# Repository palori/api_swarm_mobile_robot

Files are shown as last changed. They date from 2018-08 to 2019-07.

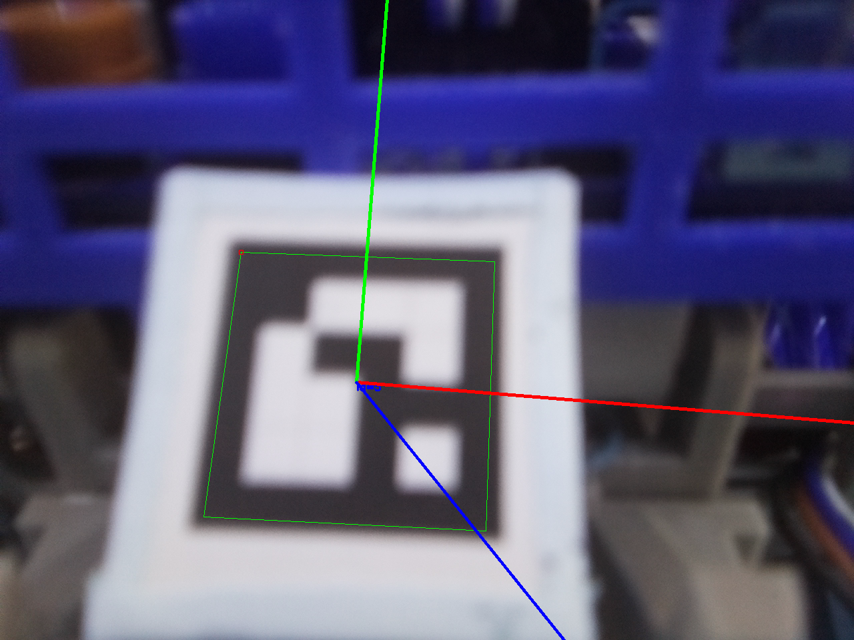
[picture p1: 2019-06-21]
API_rpi/image_proc/tests/aruco_test/pics/aruco_detected_12.png

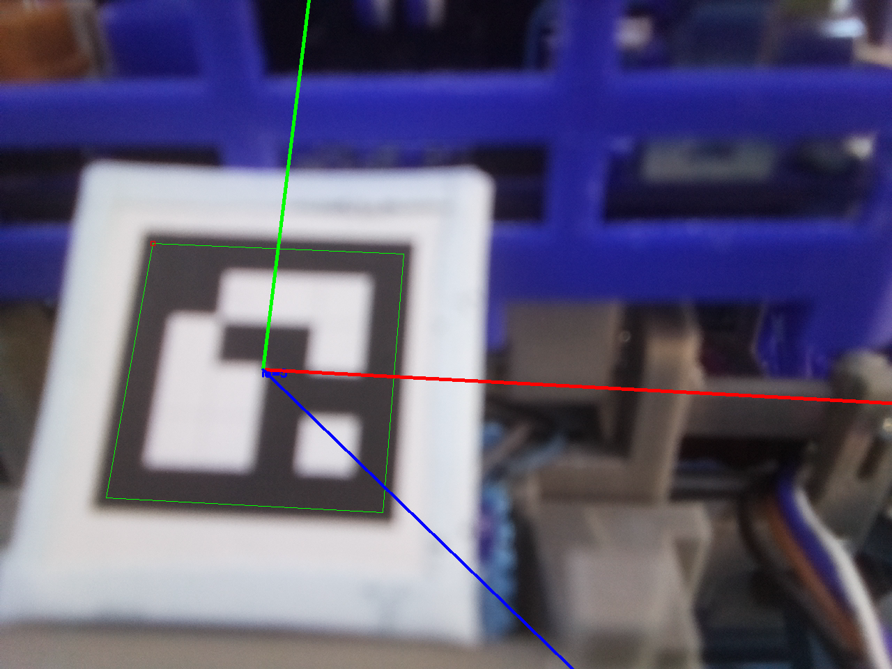
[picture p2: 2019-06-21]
API_rpi/image_proc/tests/aruco_test/pics/aruco_detected_11.png

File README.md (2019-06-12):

# api_swarm_mobile_robot
MSc Thesis: Multiple-mobile robot system.<br>
Institution: DenmarK Technical University (DTU)<br>
<br>
Authors:<br>
- Pau López Ribas<br>
- Imma Martínez Sellarès<br>
- Andrija Drk<br>
<br>
The project consists of designing. building and programming a multiple mobile robot system. It is developed to be 3 robots but it can easily be scaled up to more units.<br>
<br>
The project consists about:<br>
- `drawings` the design of the structure of the robots and the analysis of the forces<br>
- `hardware` physical components that form each robot<br>
- `software` the logic of the robots<br>
<br>

## Drawings
(still to write about)<br>
<br>

## Hardware
The hardware ... (still to work on it)<br>
2 boards<br>
Low level board: interaction with sensors (2 IR, 1 IMU, 2 encoders...)
                 and actuators (2 motors, 2 servos...)<br>
<br>

## Software
The software is divided in 2 groups (one for each board):<br>
- low-level<br>
- high-level<br>
<br>

## Matlab
...<br>
<br>

## Documents
...<br>
<br>

## Setup
Refer to the `readme.md` of the `setup` folder.<br>
<br>

## Executables
Refer to the `readme.md` of each executables folder.<br>
<br>

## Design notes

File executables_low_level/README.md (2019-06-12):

# Executables low-level board
...<br>
<br>
main_low_level.ino<br>
test folders arduino (now called `test_teensy_robot`)

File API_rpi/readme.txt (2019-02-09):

"pins.h" has nothing yet. Will contain the pins used in the Raspberry Pi.

"/demos_n_tests" contain examples you can run to test the libraries.

"/trash" contain old codes that are not used any more but than we would like to keep for some time.

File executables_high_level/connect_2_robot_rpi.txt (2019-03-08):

########################
# Connect to robot rpi #
########################

######################################################
## Useful links

- RSE WIKI, DTU Elektro Automation and Control department
  http://rsewiki.elektro.dtu.dk/index.php/Vision_based_Line_Follower

- Change Linux hostname
  https://www.howtogeek.com/167195/how-to-change-your-raspberry-pi-or-other-linux-devices-hostname/

- Mounting and unmounting using sshfs
  Mounnting is explained in a simplier way in some of the links from 'rse.wiki'
  https://help.ubuntu.com/community/SSHFS

######################################################
## Conect from a local network (hotspot...)

1. Turn on hotspot (now only in Pau's phone)

2. Connect the PC to that network

3. Check that at least 2 devices are connected (1 PC and at least 1 robot)
   - can check using ping:
     ping 192.168.43.N
                     138
                     38
                     174
                     ...

4. SSH the robot
   ssh -X user@192.168.43.N
   where user is the username of the robot (pi, local...)
   Introduce the password when asked for (egg, grenen, raspberry...)

5. Navigate to the folder where you have the script, compile it and run it
   cd ~/api_swarm_mobile_robot/API_rpi/image_proc/tests/detect_line		(might be another one)
   ls
   cmake .
   make
   ls 					(looking for the executable file to run, usually the green one)
   ./executable_file	(run the executable)

######################################################
## Conect from a local network (hotspot...)

1. Turn on hotspot (now only in Pau's phone)

2. Connect the PC to that network

3. Check that at least 2 devices are connected (1 PC and at least 1 robot)
   - can check using ping:
     ping 192.168.43.N
                     138
                     38
                     174
                     ...
          hostname.local
          cucumber.local		# cucumber would be the 'hostname' in this case
          ...

4. SSH the robot
   ssh -X user@192.168.43.N
   ssh -X user@hostname.local        # '.local' has nothing to do with the possible 'username'
   where 'user' is the username of the robot (pi, local...)
   Introduce the password when asked for (egg, grenen, raspberry...)

5. Navigate to the folder where you have the script, compile it and run it
   cd ~/api_swarm_mobile_robot/API_rpi/image_proc/tests/detect_line		(might be another one)
   ls
   cmake .
   make
   ls 					(looking for the executable file to run, usually the green one)
   ./executable_file	(run the executable)

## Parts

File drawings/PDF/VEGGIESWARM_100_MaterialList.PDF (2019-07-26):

34 | Screw M3x24 | DIN 7985 | | 4
33 | Screw M3x10 | DIN 7985 | | 4
32 | Screw M3x6 | DIN 7981 | | 34
31 | Screw M2,5x8 | DIN 7981 | | 2
30 | Screw M2,5x6 | DIN 7981 | | 16
29 | VEGGIESWARM_C113 | Rubber wheel D35 | Pololu | 5
28 | VEGGIESWARM_C112 | Axis D2 x 30 | Steel | 5
27 | VEGGIESWARM_C111 | Wheel adapter | Aluminium | 2
26 | VEGGIESWARM_C110 | Rubber wheel D90 | Pololu | 6
25 | VEGGIESWARM_C109 | Motor driver | Dual MC33926 | 1
24 | VEGGIESWARM_C108 | Plain bearing | JFM0608-04 | 2
23 | VEGGIESWARM_C107 | Battery | Lithium ion battery of 1100mAh and 12V | 1
22 | VEGGIESWARM_C106 | Motor 9.7:1 Metal Gearmotor 25Dx48L mm LP 6V with 48 CPR Encoder | Pololu | 2
21 | VEGGIESWARM_C105 | Camera Module | Raspberry Pi | 1
20 | VEGGIESWARM_C104 | IMU | MPU -6050 | 1
19 | VEGGIESWARM_C103 | Infrared sensor | Sharp 2Y0A 21F | 2
18 | VEGGIESWARM_C102 | High level board | Raspberry Pi 3 | 1
17 | VEGGIESWARM_C101 | RT Board | DTU | 1
16 | VEGGIESWARM_143_sym | Coupling 3 sym | PLA | 1
15 | VEGGIESWARM_143 | Coupling 3 | PLA | 1
14 | VEGGIESWARM_142 | Coupling 2 | PLA | 1
13 | VEGGIESWARM_141 | Coupling 1 | PLA | 1
12 | VEGGIESWARM_132_sym | Extension_sym | PLA | 1
11 | VEGGIESWARM_132 | Extension | PLA | 1
10 | VEGGIESWARM_131_sym | Extra wheels frame sym | PLA | 1
9 | VEGGIESWARM_131 | Extra wheels frame | PLA | 1
8 | VEGGIESWARM_123 | Back wheel frame | PLA | 1
7 | VEGGIESWARM_122 | Back wheel Support 2 | PLA | 1
6 | VEGGIESWARM_121 | Back wheel Support 1 | PLA | 1
5 | VEGGIESWARM_105 | Support motor driver | PLA | 1
4 | VEGGIESWARM_104 | Shell | PLA | 1
3 | VEGGIESWARM_103 | Camera support | PLA | 1
2 | VEGGIESWARM_102 | Lower frame | PLA | 1
1 | VEGGIESWARM_101 | Upper frame | PLA | 1
ITEM NO. | PART NUMBER | DESCRIPTION | MATERIAL | QTY.
Name Date Designed by IMMA 25/07/2019 Drawn by Checked by | Technical University of Denmark
Part Name Assembly Name | Project Name Design and build of a robot for the DTU RoboCup Doc Nr / Filename Scale Size A4 VEGGIESWARM_100_MaterialList

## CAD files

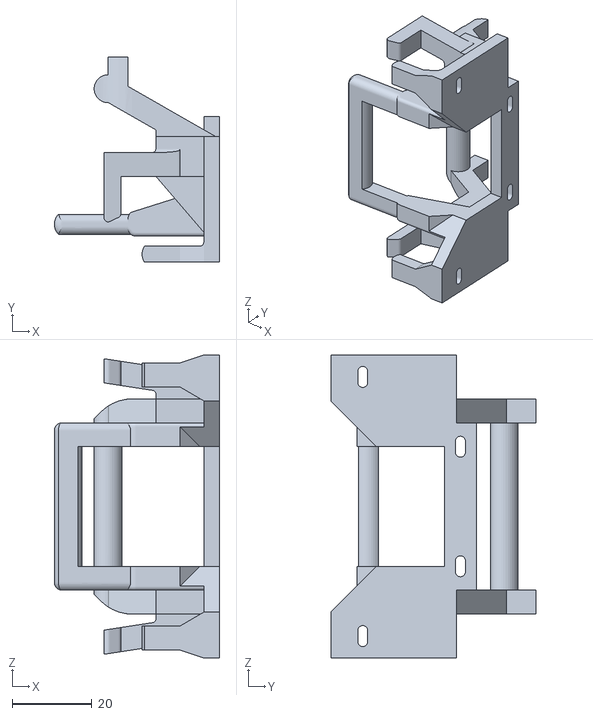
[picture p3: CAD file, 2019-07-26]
drawings/STL_Files/VEGGIESWARM_141_v4.STL
41.5 x 51.5 x 76.0

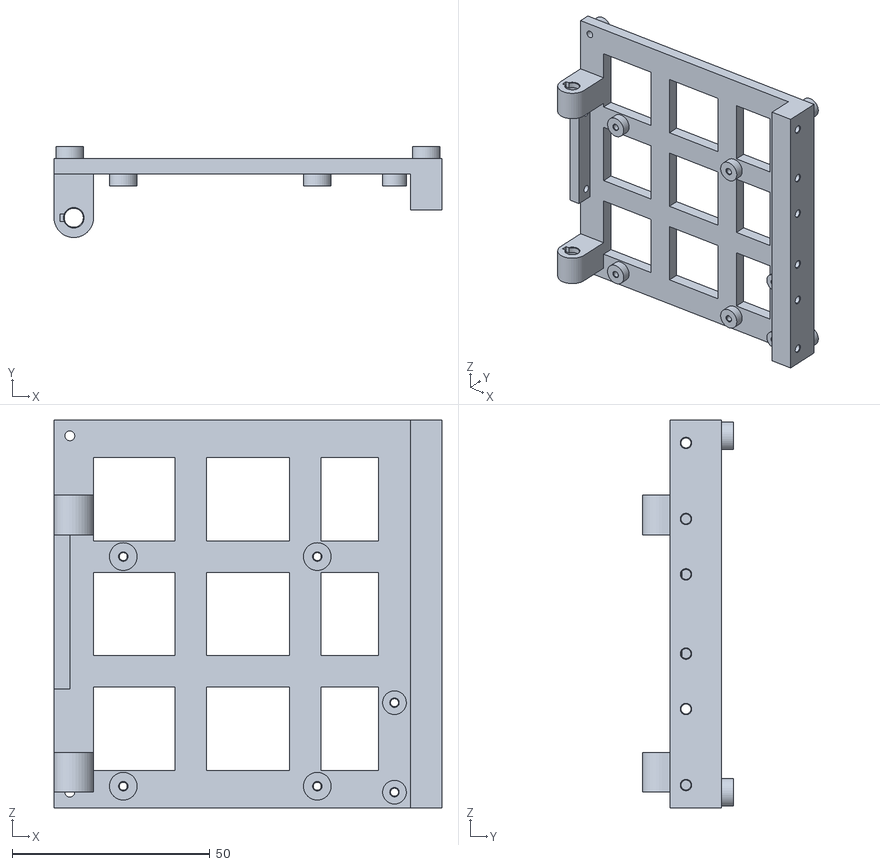
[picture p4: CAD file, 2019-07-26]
drawings/STL_Files/VEGGIESWARM_101.STL
98.0 x 23.0 x 98.0

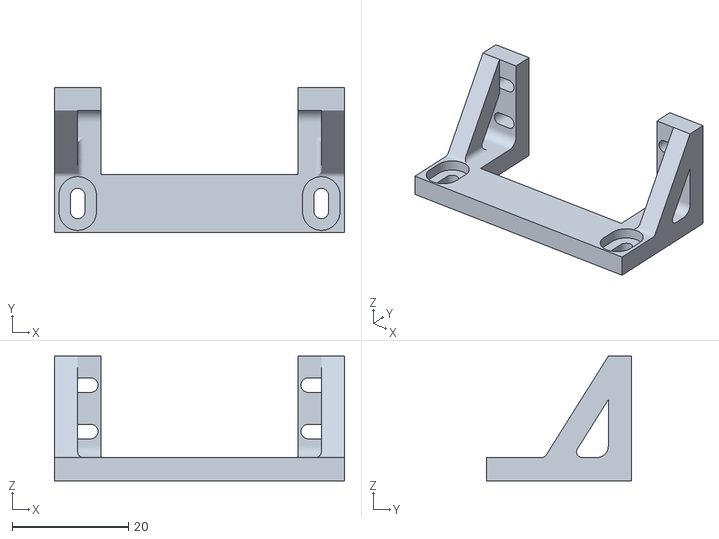
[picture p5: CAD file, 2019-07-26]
drawings/STL_Files/VEGGIESWARM_202.STL
50.0 x 25.0 x 21.5

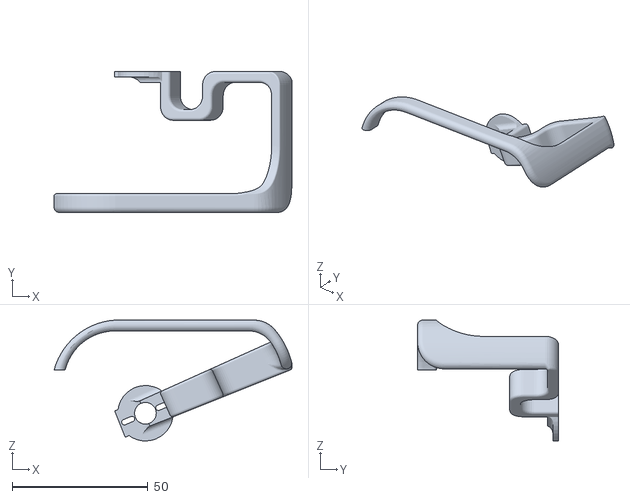
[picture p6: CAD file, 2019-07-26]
drawings/STL_Files/VEGGIESWARM_201.STL
87.7 x 52.0 x 44.5

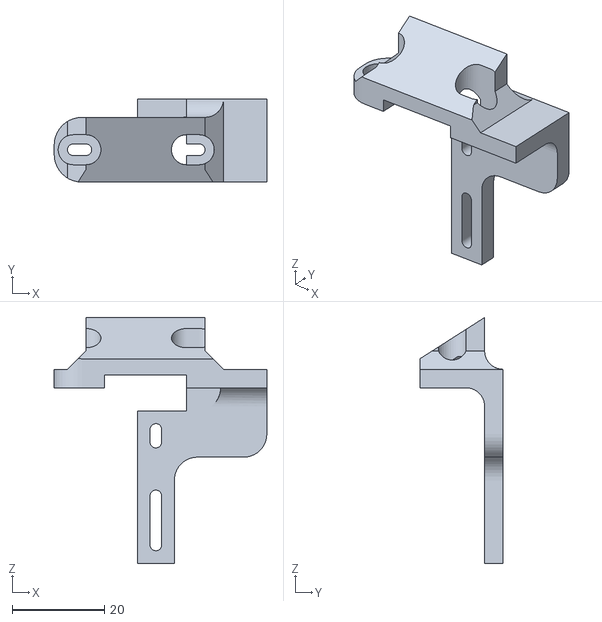
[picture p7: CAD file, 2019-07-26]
drawings/STL_Files/VEGGIESWARM_132_v1.STL
46.0 x 18.0 x 53.2

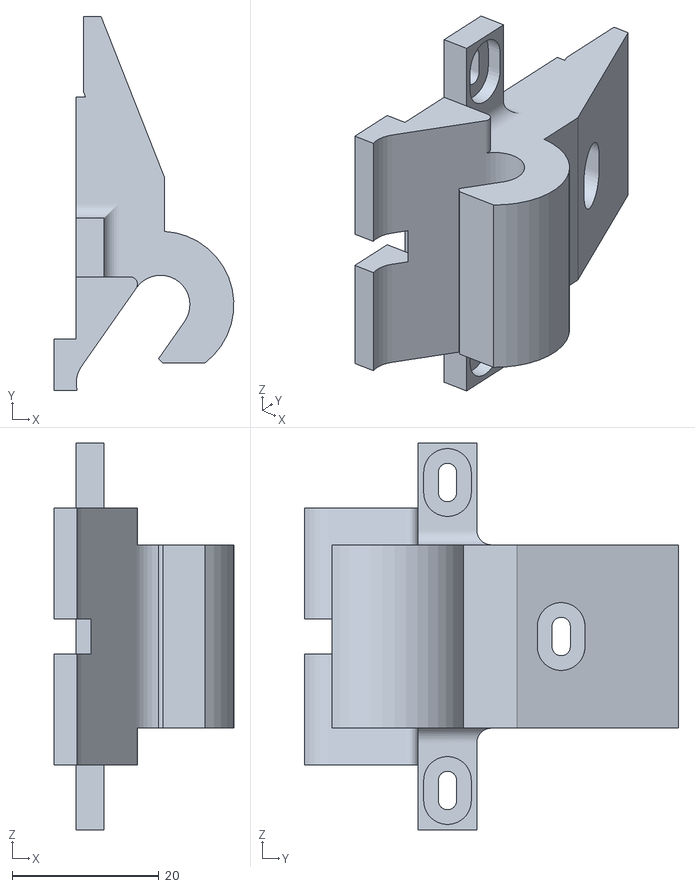
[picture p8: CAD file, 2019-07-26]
drawings/STL_Files/VEGGIESWARM_142_v4.STL
24.5 x 51.0 x 52.8

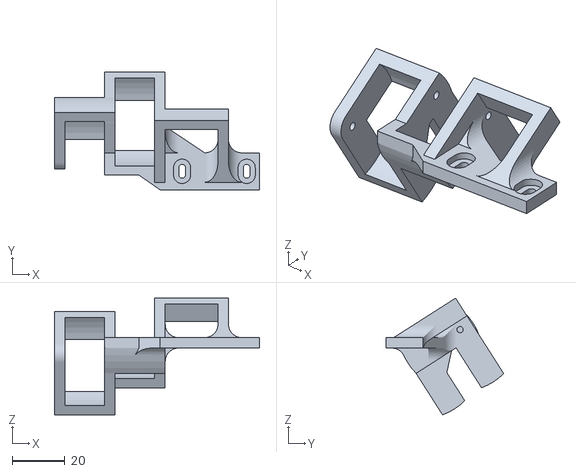
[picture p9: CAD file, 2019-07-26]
drawings/STL_Files/VEGGIESWARM_131_v3.STL
77.8 x 44.6 x 44.3

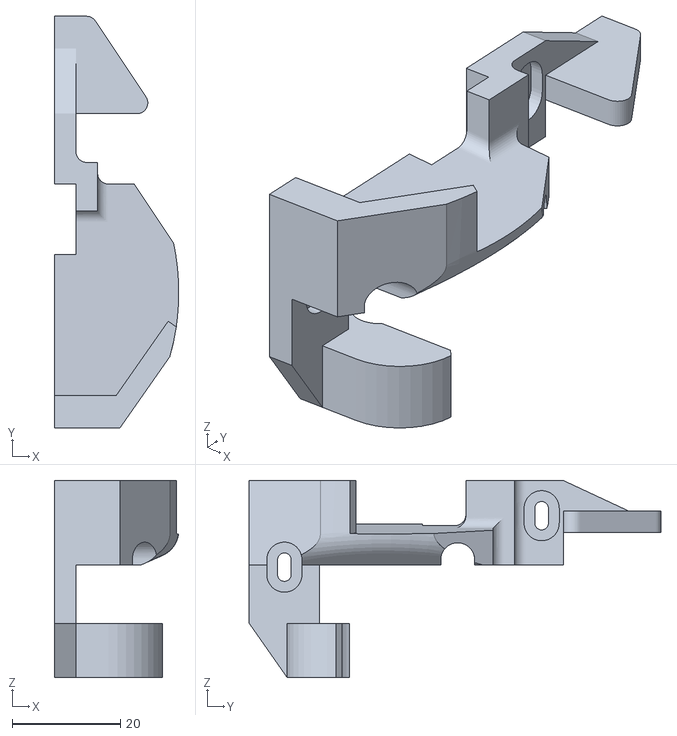
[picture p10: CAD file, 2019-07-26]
drawings/STL_Files/VEGGIESWARM_143_v4.STL
23.0 x 76.0 x 36.4

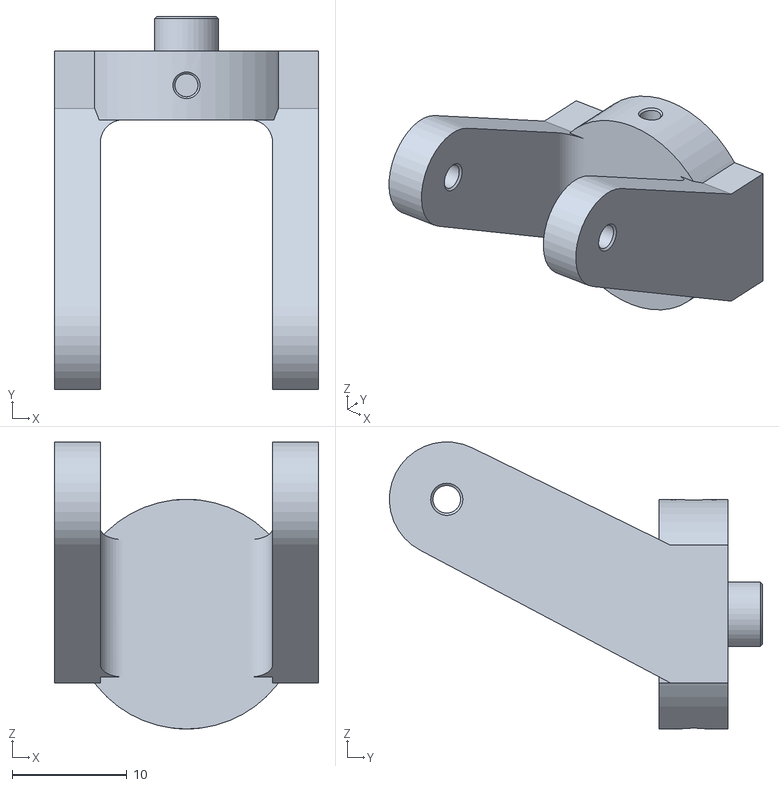
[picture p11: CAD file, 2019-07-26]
drawings/STL_Files/VEGGIESWARM_123_v3.STL
23.0 x 32.5 x 25.0

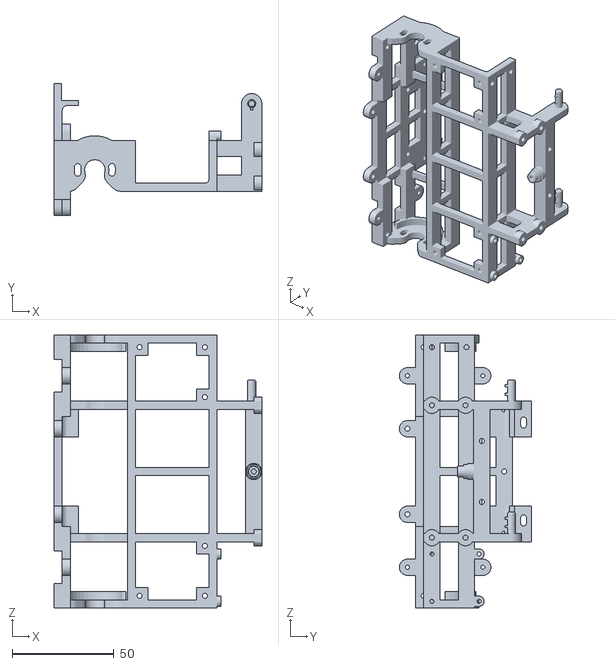
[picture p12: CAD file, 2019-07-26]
drawings/STL_Files/VEGGIESWARM_102_v3.STL
102.0 x 65.0 x 134.0

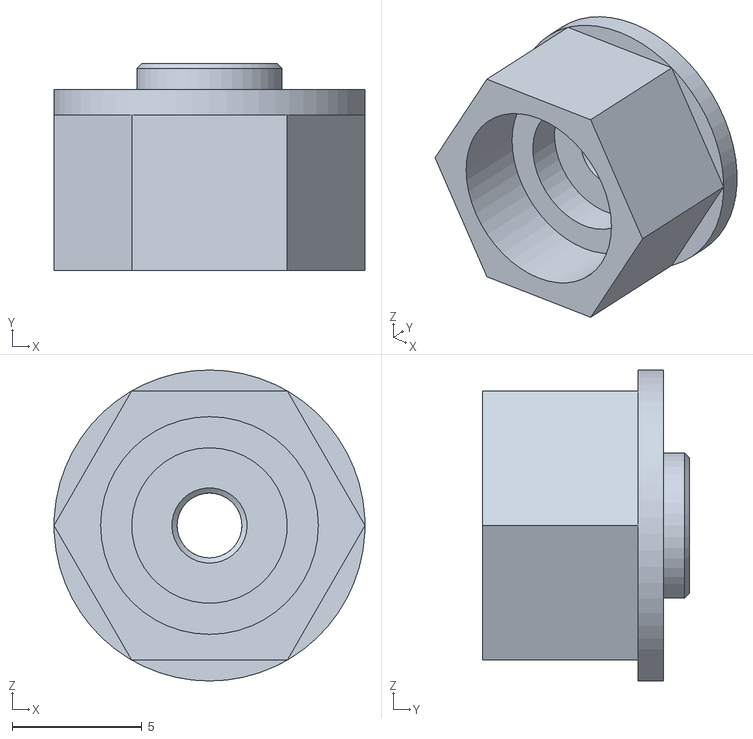
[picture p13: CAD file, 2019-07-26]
drawings/STL_Files/VEGGIESWARM_121_v3.STL
12.0 x 8.00 x 12.0

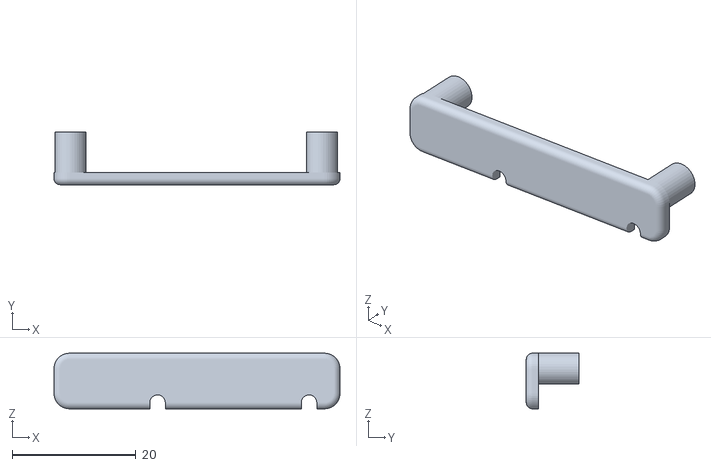
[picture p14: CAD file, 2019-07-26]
drawings/STL_Files/VEGGIESWARM_104.STL
46.2 x 8.50 x 9.00

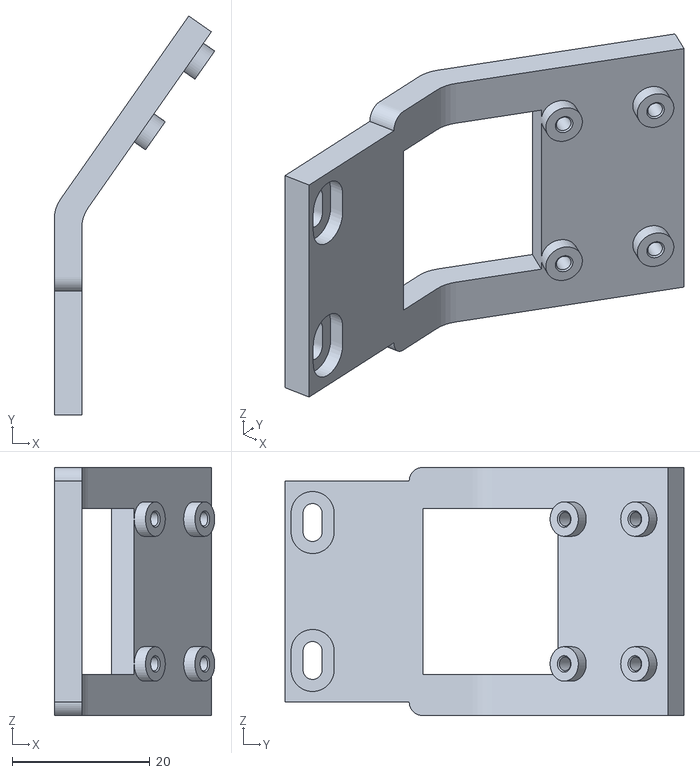
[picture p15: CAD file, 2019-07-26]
drawings/STL_Files/VEGGIESWARM_103_v1.STL
23.3 x 57.9 x 36.0

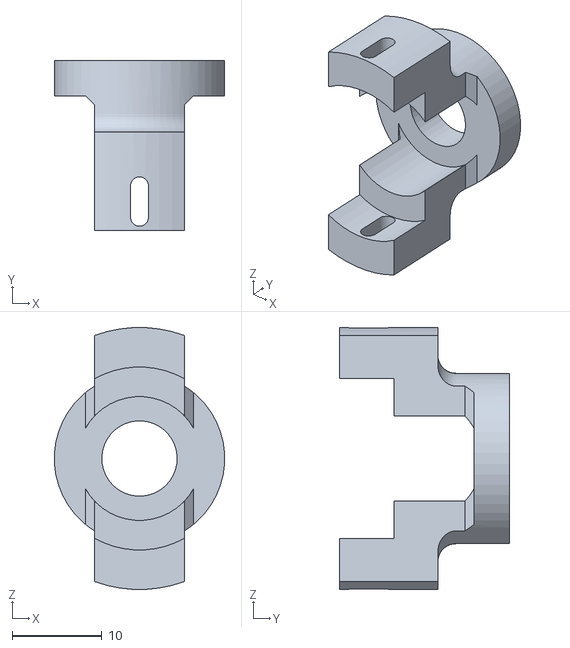
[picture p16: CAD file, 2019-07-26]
drawings/STL_Files/VEGGIESWARM_122_v4.STL
19.0 x 19.0 x 29.2

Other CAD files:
drawings/STL_Files/VEGGIESWARM_143_v4_sym.STL
drawings/STL_Files/VEGGIESWARM_131_v3_sym.STL

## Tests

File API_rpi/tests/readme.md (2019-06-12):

# Tests
The paths to the files in the `Makefile` / `CMakeLists.txt` for each test must be updated. It will not compile now :)<br>
<br>
Also bear in mind that some functions from the libraries might have been updated and might remain unchanged in the tests making them fail when attempting to compile.

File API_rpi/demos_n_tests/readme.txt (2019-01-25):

**************
* readme.txt *
**************

Run shell scripts to compile and run the tests from the terminal.
(Eg.: sh filename.sh)

To make it executable just type in the terminal:
chmod +x filename.sh

Then you will be able to run it also with this command:
./filename

It automatically deletes the executable files after showing the results in the terminal to keep the folder organized.
If the demo/test contains a while true, then the 'executable' is moved to the folder "/executables".

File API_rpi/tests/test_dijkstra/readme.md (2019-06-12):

# Test Dijkstra
Not working due to some changes in how to call the functions.<br>
Only need to be changed `main_dijkstra.cpp`.

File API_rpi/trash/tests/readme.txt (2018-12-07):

**************
* readme.txt *
**************

Run shell scripts to compile and run the tests from the terminal.
(Eg.: sh my_script.sh) 

It automatically deletes the executable files after showing the results in the terminal to keep the folder organized.

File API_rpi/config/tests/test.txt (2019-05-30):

name, task_type, num_robots
take_picture, 1, 1
up-stairs, 2, 3

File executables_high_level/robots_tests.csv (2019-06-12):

agent | id | hostname | ip | port_info | port_image | port_task
master | 0 | ginger | localhost | 7999 | 7998 | 7997
robot | 1 | ginger | localhost | 8000 | 7000 | 7010
robot | 2 | ginger | localhost | 8001 | 7001 | 7011
robot | 3 | ginger | localhost | 8002 | 7002 | 7012
# last row is never read

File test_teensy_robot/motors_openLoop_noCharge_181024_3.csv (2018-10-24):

Time | Vel1 | Vel2 | SP1 | SP2 | Out1 | Out2
18.82 | 0.00 | 0.00 | 0.10 | 0.10 | 0.40 | 0.40
19.83 | 0.00 | 0.00 | 0.10 | 0.10 | 0.40 | 0.40
19.84 | 0.00 | 0.00 | 0.10 | 0.10 | 0.40 | 0.40
19.85 | 0.00 | 0.06 | 0.10 | 0.10 | 0.40 | 0.40
19.86 | 0.00 | 0.00 | 0.10 | 0.10 | 0.40 | 0.40
19.87 | 0.00 | 0.00 | 0.10 | 0.10 | 0.40 | 0.40
19.89 | 0.00 | 0.00 | 0.10 | 0.10 | 0.40 | 0.40
19.90 | 0.00 | 0.00 | 0.10 | 0.10 | 0.40 | 0.40
19.91 | 0.00 | 0.00 | 0.10 | 0.10 | 0.40 | 0.40
19.92 | 0.00 | 0.00 | 0.10 | 0.10 | 0.40 | 0.40
19.93 | 0.00 | 0.00 | 0.10 | 0.10 | 0.40 | 0.40
19.94 | 0.00 | 0.00 | 0.10 | 0.10 | 0.40 | 0.40
19.95 | 0.00 | 0.00 | 0.10 | 0.10 | 0.40 | 0.40
19.96 | 0.00 | 0.00 | 0.10 | 0.10 | 0.40 | 0.40
19.97 | 0.00 | 0.00 | 0.10 | 0.10 | 0.40 | 0.40
19.98 | 0.00 | 0.00 | 0.10 | 0.10 | 0.40 | 0.40
19.99 | 0.00 | 0.00 | 0.10 | 0.10 | 0.40 | 0.40
20.00 | 0.00 | 0.00 | 0.10 | 0.10 | 0.40 | 0.40
20.01 | 0.00 | 0.00 | 0.10 | 0.10 | 0.40 | 0.40
20.02 | 0.00 | 0.00 | 0.10 | 0.10 | 0.40 | 0.40
20.03 | 0.00 | 0.00 | 0.10 | 0.10 | 0.40 | 0.40
20.04 | 0.00 | 0.00 | 0.10 | 0.10 | 0.40 | 0.40
20.05 | 0.00 | 0.00 | 0.10 | 0.10 | 0.40 | 0.40
20.06 | 0.00 | 0.00 | 0.10 | 0.10 | 0.40 | 0.40
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

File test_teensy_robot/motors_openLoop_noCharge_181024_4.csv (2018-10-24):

Time | Vel1 | Vel2 | SP1 | SP2 | Out1 | Out2
14.40 | 0.00 | 0.00 | 0.10 | 0.10 | 0.10 | 0.10
15.41 | 0.00 | 0.00 | 0.10 | 0.10 | 0.10 | 0.10
15.42 | 0.00 | 0.00 | 0.10 | 0.10 | 0.10 | 0.10
15.43 | 0.00 | 0.00 | 0.10 | 0.10 | 0.10 | 0.10
15.44 | 0.00 | 0.00 | 0.10 | 0.10 | 0.10 | 0.10
15.45 | 0.00 | 0.00 | 0.10 | 0.10 | 0.10 | 0.10
15.46 | 0.00 | 0.00 | 0.10 | 0.10 | 0.10 | 0.10
15.47 | 0.00 | 0.00 | 0.10 | 0.10 | 0.10 | 0.10
15.48 | 0.00 | 0.00 | 0.10 | 0.10 | 0.10 | 0.10
15.49 | 0.00 | 0.00 | 0.10 | 0.10 | 0.10 | 0.10
15.50 | 0.00 | 0.00 | 0.10 | 0.10 | 0.10 | 0.10
15.51 | 0.00 | 0.00 | 0.10 | 0.10 | 0.10 | 0.10
15.52 | 0.00 | 0.00 | 0.10 | 0.10 | 0.10 | 0.10
15.53 | 0.00 | 0.00 | 0.10 | 0.10 | 0.10 | 0.10
15.54 | 0.00 | 0.00 | 0.10 | 0.10 | 0.10 | 0.10
15.55 | 0.00 | 0.00 | 0.10 | 0.10 | 0.10 | 0.10
15.56 | 0.00 | 0.00 | 0.10 | 0.10 | 0.10 | 0.10
15.57 | 0.00 | 0.00 | 0.10 | 0.10 | 0.10 | 0.10
15.58 | 0.00 | 0.00 | 0.10 | 0.10 | 0.10 | 0.10
15.59 | 0.00 | 0.00 | 0.10 | 0.10 | 0.10 | 0.10
15.60 | 0.00 | 0.00 | 0.10 | 0.10 | 0.10 | 0.10
15.61 | 0.00 | 0.00 | 0.10 | 0.10 | 0.10 | 0.10
15.62 | 0.00 | 0.00 | 0.10 | 0.10 | 0.10 | 0.10
15.64 | 0.00 | 0.00 | 0.10 | 0.10 | 0.10 | 0.10
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

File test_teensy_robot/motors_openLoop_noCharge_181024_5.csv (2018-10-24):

Time | Vel1 | Vel2 | SP1 | SP2 | Out1 | Out2
7.36 | 0.00 | 0.00 | 0.10 | 0.10 | 0.40 | 0.40
8.37 | 0.00 | 0.00 | 0.10 | 0.10 | 0.40 | 0.40
8.38 | 0.00 | 0.06 | 0.10 | 0.10 | 0.40 | 0.40
8.39 | 0.00 | 0.11 | 0.10 | 0.10 | 0.40 | 0.40
8.40 | 0.00 | 0.00 | 0.10 | 0.10 | 0.40 | 0.40
8.41 | 0.00 | 0.12 | 0.10 | 0.10 | 0.40 | 0.40
8.42 | 0.00 | 0.11 | 0.10 | 0.10 | 0.40 | 0.40
8.43 | 0.00 | 0.12 | 0.10 | 0.10 | 0.40 | 0.40
8.44 | 0.00 | 0.18 | 0.10 | 0.10 | 0.40 | 0.40
8.45 | 0.00 | 0.11 | 0.10 | 0.10 | 0.40 | 0.40
8.46 | 0.00 | 0.12 | 0.10 | 0.10 | 0.40 | 0.40
8.47 | 0.00 | 0.18 | 0.10 | 0.10 | 0.40 | 0.40
8.48 | 0.00 | 0.11 | 0.10 | 0.10 | 0.40 | 0.40
8.49 | 0.00 | 0.18 | 0.10 | 0.10 | 0.40 | 0.40
8.50 | 0.00 | 0.12 | 0.10 | 0.10 | 0.40 | 0.40
8.51 | 0.00 | 0.17 | 0.10 | 0.10 | 0.40 | 0.40
8.52 | 0.00 | 0.12 | 0.10 | 0.10 | 0.40 | 0.40
8.53 | 0.00 | 0.17 | 0.10 | 0.10 | 0.40 | 0.40
8.54 | 0.00 | 0.18 | 0.10 | 0.10 | 0.40 | 0.40
8.55 | 0.00 | 0.12 | 0.10 | 0.10 | 0.40 | 0.40
8.56 | 0.00 | 0.17 | 0.10 | 0.10 | 0.40 | 0.40
8.57 | 0.00 | 0.18 | 0.10 | 0.10 | 0.40 | 0.40
8.58 | 0.00 | 0.12 | 0.10 | 0.10 | 0.40 | 0.40
8.59 | 0.00 | 0.17 | 0.10 | 0.10 | 0.40 | 0.40
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

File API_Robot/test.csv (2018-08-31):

A | 1
b | 2
d | 40

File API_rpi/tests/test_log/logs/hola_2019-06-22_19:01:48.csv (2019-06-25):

1561222908181 | Bon dia!
1561222908181 | Bona nit :)

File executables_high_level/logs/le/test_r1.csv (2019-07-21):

timestamp | robot_id | robot_a_id | robot_b_id | robot_a_alive | robot_b_alive | leader | trigger | i_detected | is_election | robots_ids | proposed_leader
1561248971172 | 1 | 2 | 3 | 0 | 0 | 0 | 1 | 0 | 0
1561248971423 | 1 | 2 | 3 | 0 | 0 | 1 | 0 | 0 | 0
1561248971673 | 1 | 2 | 3 | 0 | 0 | 1 | 0 | 0 | 0
1561248971923 | 1 | 2 | 3 | 0 | 0 | 1 | 0 | 0 | 0
1561248972173 | 1 | 2 | 3 | 1 | 1 | 1 | 1 | 0 | 0 | 3 | 1
1561248972424 | 1 | 2 | 3 | 1 | 1 | 1 | 1 | 0 | 0 | 3;1;2 | 1
1561248972674 | 1 | 2 | 3 | 1 | 1 | 1 | 1 | 0 | 0 | 3;1;2 | 1
1561248972924 | 1 | 2 | 3 | 1 | 1 | 1 | 1 | 0 | 0 | 3;1;2 | 1
1561248973174 | 1 | 2 | 3 | 1 | 1 | 1 | 1 | 0 | 0 | 3;1;2 | 1
1561248973425 | 1 | 2 | 3 | 1 | 1 | 1 | 1 | 0 | 0 | 3;1;2 | 1
1561248973675 | 1 | 2 | 3 | 1 | 1 | 1 | 1 | 0 | 0 | 3;1;2 | 1
1561248973925 | 1 | 2 | 3 | 1 | 1 | 1 | 1 | 0 | 0 | 3;1;2 | 1
1561248974175 | 1 | 2 | 3 | 1 | 1 | 1 | 1 | 0 | 0 | 3;1;2 | 1
1561248974425 | 1 | 2 | 3 | 1 | 1 | 1 | 0 | 0 | 0
1561248974676 | 1 | 2 | 3 | 1 | 1 | 1 | 0 | 0 | 0
1561248974926 | 1 | 2 | 3 | 1 | 1 | 1 | 0 | 0 | 0
1561248975176 | 1 | 2 | 3 | 1 | 1 | 1 | 0 | 0 | 0
1561248975426 | 1 | 2 | 3 | 1 | 1 | 1 | 0 | 0 | 0
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

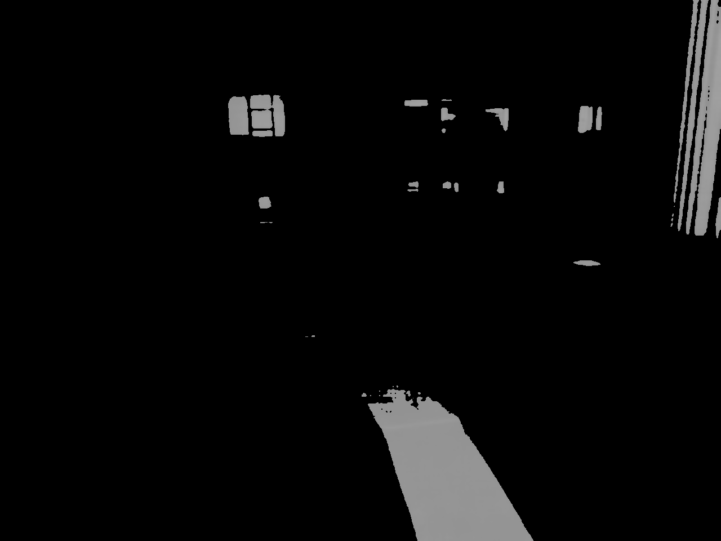
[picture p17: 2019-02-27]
API_rpi/image_proc/tests/images/img_bin_ycbcr2.png

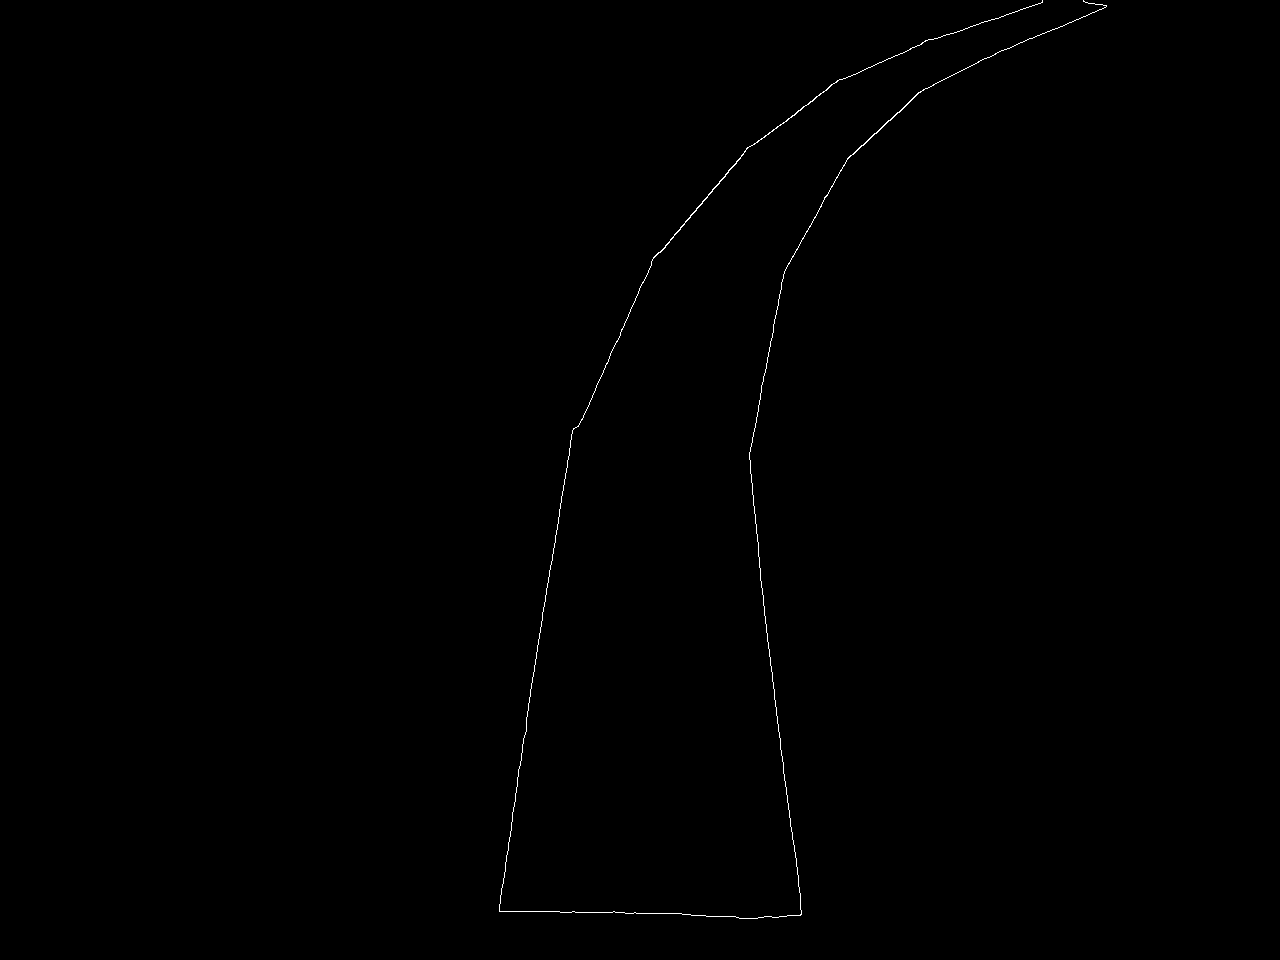
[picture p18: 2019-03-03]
API_rpi/image_proc/tests/images/img_edge.png

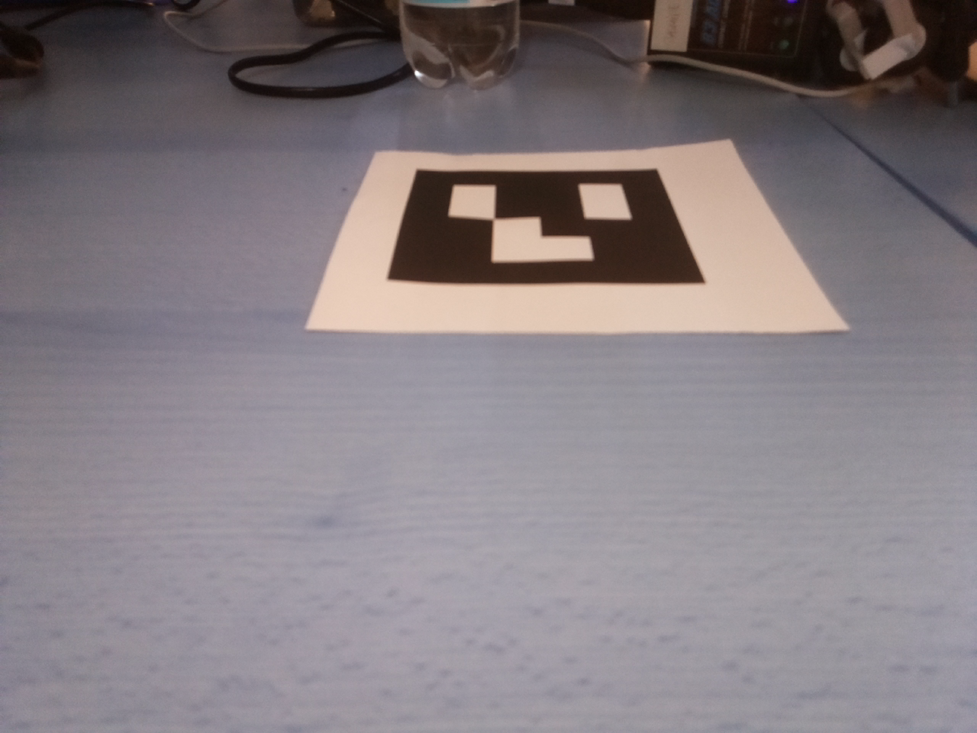
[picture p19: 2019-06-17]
API_rpi/image_proc/tests/aruco_test/pics/aruco_0.png

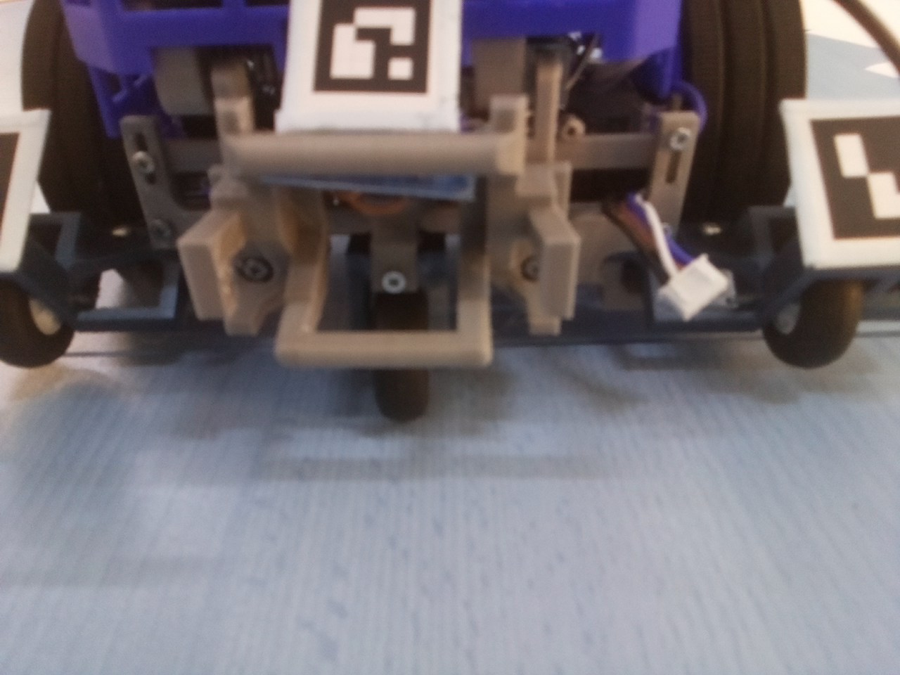
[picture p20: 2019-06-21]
API_rpi/image_proc/tests/aruco_test/pics/aruco_detected_5.png

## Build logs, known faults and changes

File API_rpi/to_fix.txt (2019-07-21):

To fix
------
sensors.x (item -> items)
attr & methods -> public and private

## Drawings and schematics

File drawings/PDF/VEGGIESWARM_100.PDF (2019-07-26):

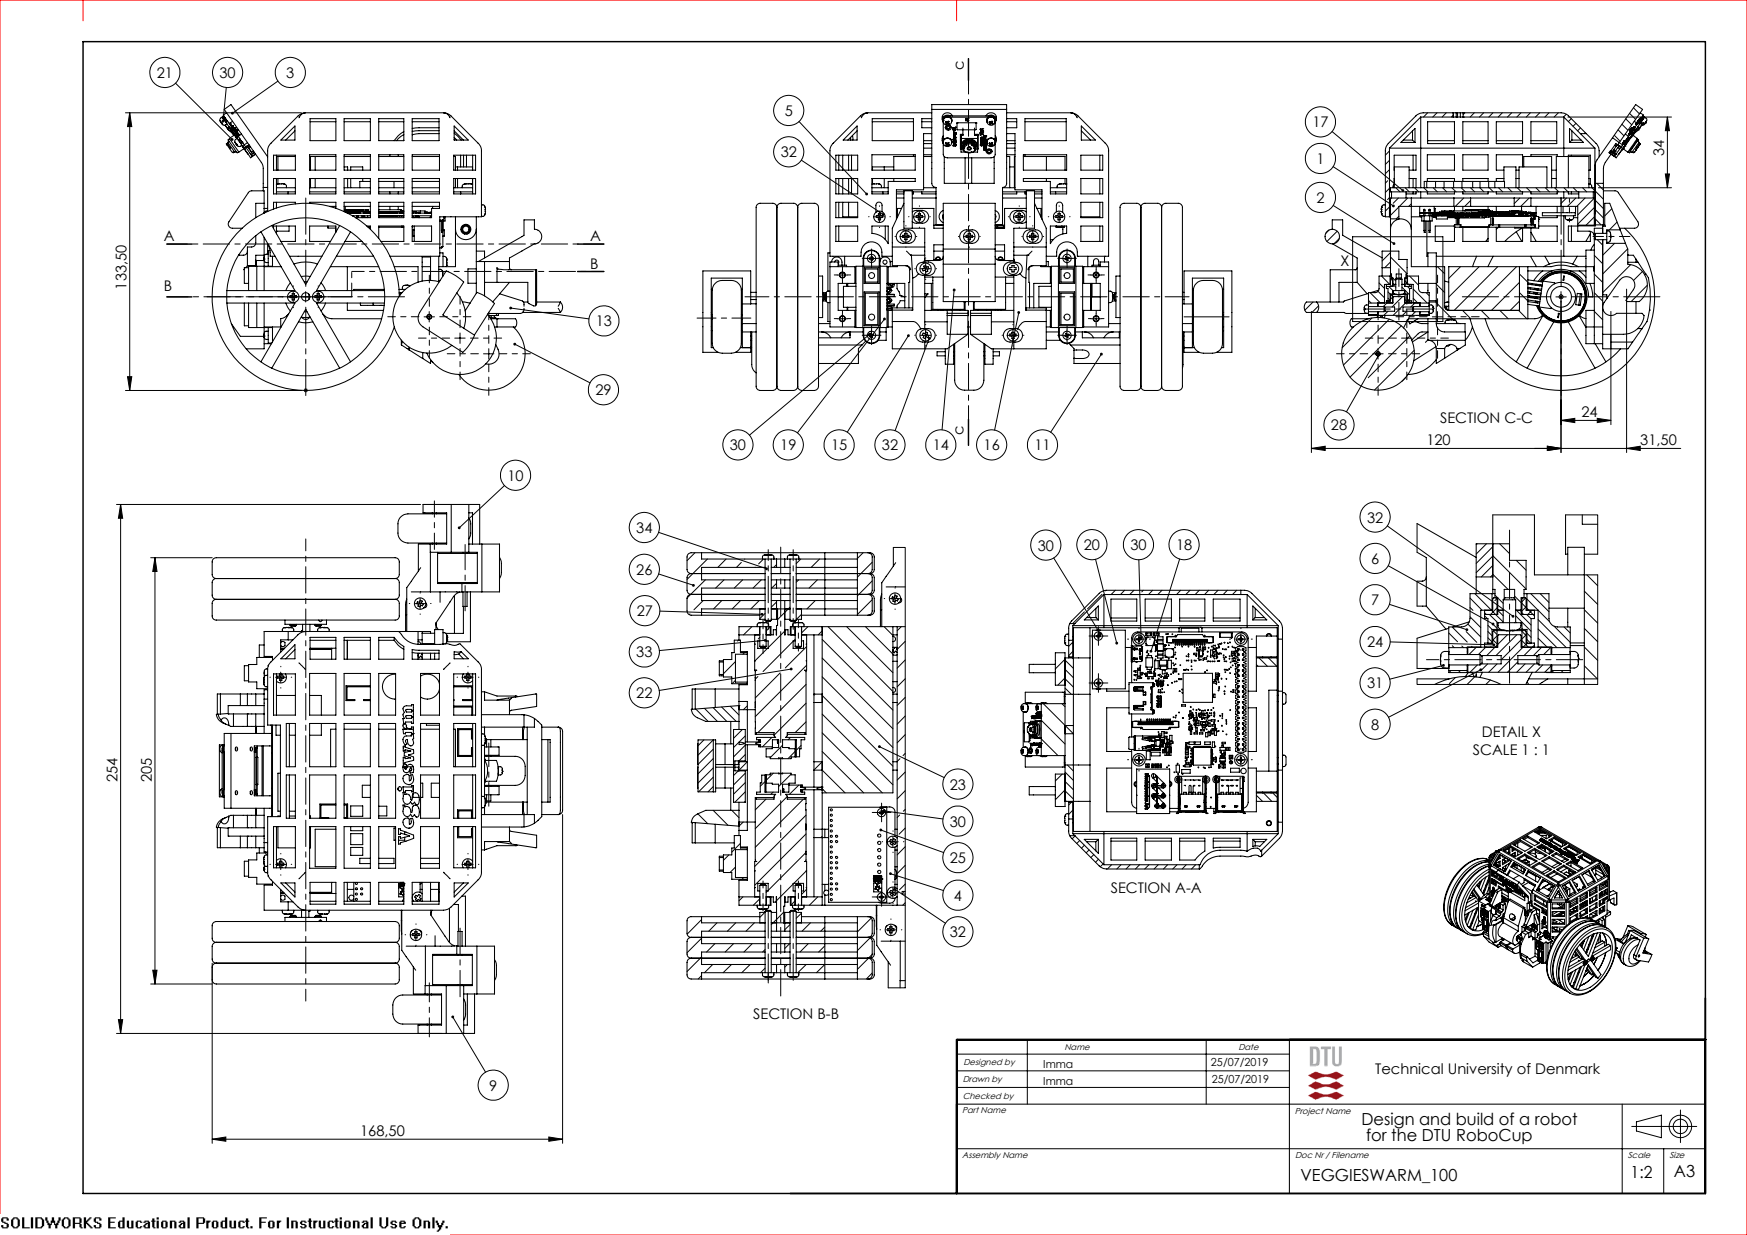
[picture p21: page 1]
SECTION A-A; SECTION C-C; SECTION B-B; DETAIL X SCALE 1 : 1; Assembly Name; Part Name; Checked by; Drawn by; Designed by; Technical University of Denmark Imma

Project Name
Design and build of a robot
for the DTU RoboCup
VEGGIESWARM_100

Doc Nr / Filename

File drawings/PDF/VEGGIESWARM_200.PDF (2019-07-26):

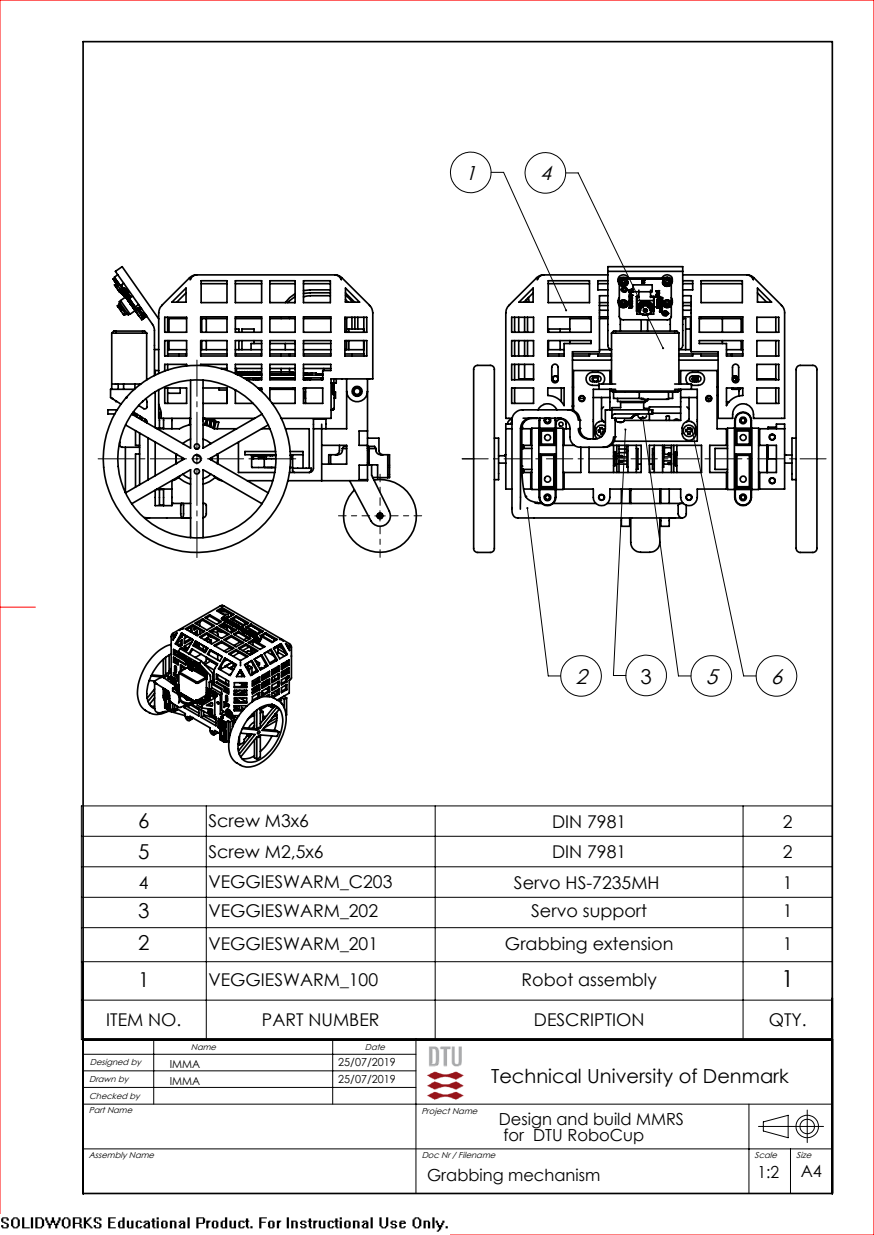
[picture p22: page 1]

6 | Screw M3x6 | DIN 7981 | 2
5 | Screw M2,5x6 | DIN 7981 | 2
4 | VEGGIESWARM_C203 | Servo HS-7235MH | 1
3 | VEGGIESWARM_202 | Servo support | 1
2 | VEGGIESWARM_201 | Grabbing extension | 1
1 | VEGGIESWARM_100 | Robot assembly | 1
ITEM NO. | PART NUMBER | DESCRIPTION | QTY.

Name Date Designed by IMMA 25/07/2019 IMMA 25/07/2019 Drawn by Checked by | Technical University of Denmark

Part Name Assembly Name | Project Name Design and build MMRS for DTU RoboCup Doc Nr / Filename Scale Size A4 Grabbing mechanism 1:2

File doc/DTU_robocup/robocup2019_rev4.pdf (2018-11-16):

2 | 1 | | 3 13 | 7

### start

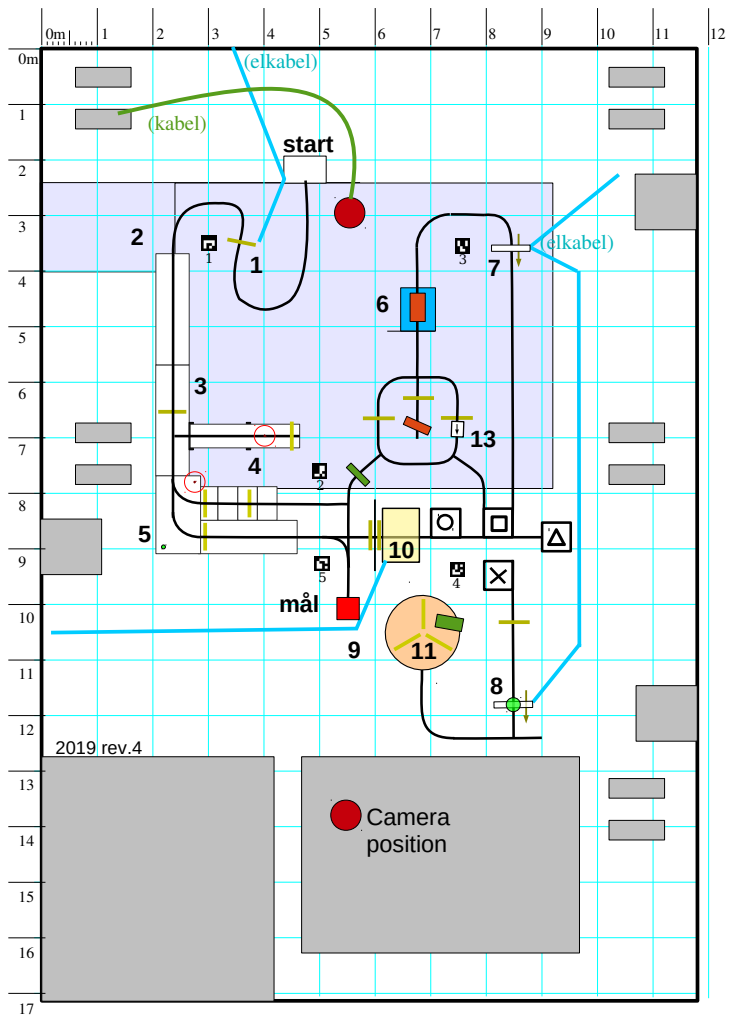
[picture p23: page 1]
2019 rev.4; mål; (elkabel); (kabel)

Camera position

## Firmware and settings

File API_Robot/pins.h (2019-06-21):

#ifndef PINS_H
#define PINS_H


#define USING_ARDUINO // flag to see if need to include Arduino library or not
// Simplier version than the original from JCA.
// Teensy 3.5
//////////////////////////////////////////////////////////////////////////////////

// Pin Definitions for Regbot v4.1 2018

//Motor names

#define LEFT_MOTOR 1
#define RIGHT_MOTOR 2

// Main pins
#define PIN_LED_STATUS          11
#define PIN_LED_DEBUG           13
#define PIN_START_BUTTON        26
#define PIN_LINE_LED_HIGH       12
#define PIN_LINE_LED_LOW        25
#define PIN_DISABLE2            7//27
#define PIN_POWER_IR            24
#define PIN_POWER_ROBOT         28

// ADC pins
#define ADC_NUM_NO_LS           5
#define ADC_NUM_ALL             (ADC_NUM_NO_LS + 8)
//
#define PIN_IR_RAW_1            A1
#define PIN_IR_RAW_2            A0
#define PIN_BATTERY_VOLTAGE     A14
#define PIN_LEFT_MOTOR_CURRENT  31//A2
#define PIN_RIGHT_MOTOR_CURRENT 32//A3
//
#define PIN_LINE_SENSOR_0       A12
#define PIN_LINE_SENSOR_1       A13
#define PIN_LINE_SENSOR_2       A15
#define PIN_LINE_SENSOR_3       A16
#define PIN_LINE_SENSOR_4       A17
#define PIN_LINE_SENSOR_5       A18
#define PIN_LINE_SENSOR_6       A19
#define PIN_LINE_SENSOR_7       A20

// Motor Controller pins
#define PIN_LEFT_DIR            37//6
#define PIN_LEFT_PWM            35//3
#define PIN_RIGHT_PWM           36//4
#define PIN_RIGHT_DIR           38//2

#define PIN_LEFT_ENCODER_A      23
#define PIN_LEFT_ENCODER_B      22
#define PIN_RIGHT_ENCODER_A     20
#define PIN_RIGHT_ENCODER_B     21
#define M1DIR           PIN_LEFT_DIR // M1IN2 - Teensy Digital (direction)
#define M1PWM           PIN_LEFT_PWM // M1IN1 - Teensy Digital (PWM)
#define M2DIR3          PIN_RIGHT_DIR // M2IN2 - Teensy Digital (direction) hardware 3 only
#define M2PWM3          PIN_RIGHT_PWM // M2IN1 - Teensy Digital (PWM) hardware 3
#define M12DIS          PIN_DISABLE2 // M1+M2 D2  enable both motors - hardware 3 only
#define M1ENC_A         PIN_LEFT_ENCODER_A // Encoder A - Teensy Digital
#define M1ENC_B         PIN_LEFT_ENCODER_B // Encoder B - Teensy Digital
#define M2ENC_A         PIN_RIGHT_ENCODER_A // Encoder A - Teensy Digital
#define M2ENC_B         PIN_RIGHT_ENCODER_B // Encoder B - Teensy Digital
// Legacy pins (only used < 3)
#define M1DIS1          4 // M1D2  - Teensy Digital 4 (disable (hiz))) - hardware < 3
#define M2DIS1          10 // M2D2  - Teensy Digital 10 (disable (hi-z)) - hardware < 3
#define M2PWM1          9 // M2IN1 - Teensy Digital 9 (PWM) hardware < 3
#define SLEW            7 // SLEW  - Teensy Digital 7  -  hardware 1 og 2 only, hardware 3 fixed high
#define M2DIR1          8 // M2IN2 - Teensy Digital 8 (direction) hardware < 3 only

// Servo pins
#define PIN_SERVO1      5 // Teensy pin for servo 1
#define PIN_SERVO2      9 // Teensy pin for servo 2
#define PIN_SERVO3      10 // Teensy pin for servo 3
#define PIN_SERVO4      29 // Teensy pin for servo 4
#define PIN_SERVO5      30 // Teensy pin for servo 5 (Shared with Buzzer!)
#define SERVO_PIN_0     PIN_SERVO4 // Deprecated!
#define SERVO_PIN_1     PIN_SERVO5 // Deprecated!
#define PIN_BUZZER		30 // Shared with SERVO5!

#endif

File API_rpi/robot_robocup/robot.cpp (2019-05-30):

#include "robot.h"

Robot::Robot(){
	//params.hostname.set("localhost");

	this->hostname_master.set("localhost");

	Robot_params rp("test",1,2,3,4,5,10);
	this->params = rp;

	/*Publisher pub(this->params.port_image.get());
	pub.disconnect();
	pub_image_task = pub;
	pub_image_task.setup();

	Publisher pub1(this->params.port_info.get());
	pub1.disconnect();
	pub_robot_info = pub1;
	pub_robot_info.setup();*/

	//pub_image_task(this->params.port_image.get());
	//pub_robot_info(this->params.port_info.get());

	pub_image_task.set_port(this->params.port_image.get());
	pub_image_task.setup();

	pub_robot_info.set_port(this->params.port_image.get());
	pub_robot_info.setup();

	run_mission.set(false);
}

Robot::~Robot(){}


/*/ probably never used...
Robot::Robot(string hostname){ // params from other 2 robots (port and hostname)
	//Subscriber subs_robot_a();
	//Subscriber subs_robot_b();
	Robot_params rp(hostname,5000,20);
	this->params = rp;
	//this->params(hostname,1,2,3,4,5,10);
	//params.hostname.set(hostname);
	//cout << "hostname: " << this->params.hostname.get_last_item() << endl;

}*/

// always use this one
Robot::Robot(string hostname_master, string hostname, string hostname_a, string hostname_b, int max_len, int port_image, int port_task, int port_info, int port_info_robot_a, int port_info_robot_b){
	//cout << "start robot constructor" << endl;
	this->hostname_master.set(hostname_master);

	Robot_params rp(hostname, port_image, port_task, port_info, port_info_robot_a, port_info_robot_b,max_len);
	this->params = rp;
	//cout << "this params done" << endl;
	
	Robot_params rp_a(hostname_a, port_info_robot_a, max_len);
	this->robot_a = rp_a;

	Robot_params rp_b(hostname_b, port_info_robot_b, max_len);
	this->robot_b = rp_b;



	/*
	Publisher pub(this->params.port_image.get());
	pub.disconnect();
	pub_image_task = pub;
	pub_image_task.setup();

	Publisher pub1(this->params.port_info.get());
	pub1.disconnect();
	pub_robot_info = pub1;
	pub_robot_info.setup();
	*/

	//pub_image_task(this->params.port_image.get());
	//pub_robot_info(this->params.port_info.get());

	pub_image_task.set_port(this->params.port_task.get());
	pub_image_task.setup();

	pub_robot_info.set_port(this->params.port_info.get());
	pub_robot_info.setup();

	run_mission.set(false);
	
}




void Robot::serial(){

	// may want to send some initialization
	// params like: wheel diameter, dist btw wheels, gearbox ratio...

	string msg_master = "", old_msg_master = "1";
	string update_pose = "", old_update_pose = "";
	string msg_image = "", old_msg_image = "";
	string msg_drive = "", old_msg_drive = "";
	string data = "";

	string QWERT = "qwert";
	master_data.set(QWERT);
	init_pose.set(QWERT);
	drive_command.set(QWERT);
	image_data.set(QWERT);

	serial_comm.serial_open();
	int count = 0, millis = 50;
	while(true){

		//if(run_mission.get()){

			//---------------WRITING SERIAL---------------//
			count ++;
			
			// update msg
			msg_master = master_data.get();
			update_pose = init_pose.get();
			msg_drive = drive_command.get();
			msg_image = image_data.get();

			if (msg_master != QWERT) {
				serial_comm.serial_write(msg_master);
				//cout << "master msg: " << msg_master << endl;
				master_data.set(QWERT);
			}
			else if (update_pose != QWERT) {
				serial_comm.serial_write(update_pose);
				cout << "init_pose: " << update_pose << endl;
				init_pose.set(QWERT);
			}
			else if (msg_drive != QWERT) {
				serial_comm.serial_write(msg_drive);
				//cout << "drive msg: " << msg_drive << endl;
				drive_command.set(QWERT);
			}
			else if (msg_image != QWERT) {
				serial_comm.serial_write(msg_image);
				//cout << "image msg: " << msg_image << endl;
				image_data.set(QWERT);
			}
			
			
			//int millis_sleep = 50;
			//this_thread::sleep_for(chrono::milliseconds(millis_sleep));
		/*}
		else{
			if (msg_master != old_msg_master) {
				// Maybe send to stop --> ask Andrija
				cout << "Should send STOP to Teensy, but not implemented yet!" << endl;
				old_msg_master = msg_master;
			}
		}*/

		//---------------READING SERIAL---------------//
		// Commented for testing in Pau's pc
		//cout << "reading serial..." << endl;
		data = serial_comm.serial_read();
		//cout << "\n*******\nserial data: " << data << "\n*******\n";
		decode_sensors(data, sensors);
		
		/*if (count>= 1000){		// DELETE! only for debuging
			cout << endl << "### new task to Teensy: " << msg << " ###" << endl << endl;
			sensors.print_info();
			count = 0;
		}*/
		//sensors.print_info();
		// save data
		// need to be decoded to be used (can be done here or in localization...)
		// maybe easier to modify 'comm_rpi_1.cpp' and do it there
		// then update 'robot_params'
		//
		int millis_sleep = 10;
		//this_thread::sleep_for(chrono::milliseconds(millis_sleep));
		cout << "X: " << sensors.x.get() << "    Y: " << sensors.y.get_last_item() << "    th: " << sensors.th.get_last_item() << endl;
		
	}
	serial_comm.serial_close();
}


void Robot::listen_image_process(){
	Subscriber subs_image_data(params.port_image.get(), "localhost");//params.hostname.get());
	string data = "", new_target;
	while(true){
		//cout << "listenning to image processing..." << endl;
		data = subs_image_data.listen();	// blocking call
		image_data.set(data);
		//cout << "image data to decode: " << data << endl;
		// decode data into params to use for localization and send to TSY
		decode_image(data, sensors);
	}
}

void Robot::listen_robot_a(){
	Subscriber subs_robot_a(robot_a.port_info.get(), robot_a.hostname.get());
	string info;
	cout << "listenning to robot " << robot_a.hostname.get() << "..." << endl;
	while(true){
		info = subs_robot_a.listen();		// blocking call
		decode_robot_params(info, robot_a);
	}

}


void Robot::listen_robot_b(){
	Subscriber subs_robot_b(robot_b.port_info.get(), robot_b.hostname.get());
	string info;
	cout << "listenning to robot " << robot_b.hostname.get() << "..." << endl;
	while(true){
		info = subs_robot_b.listen();		// blocking call
		decode_robot_params(info, robot_b);
	}

}

void Robot::listen_master(){
	string master = this->hostname_master.get();
	Subscriber subs_master(8001, master);
	string msg;
	int action = -1;
	cout << "listenning to master '" << master << "'..." << endl;
	while(true){
		msg = subs_master.listen();		// blocking call
		cout << "Master says: " << msg << endl;
		// decode info message
		//action = decode_master_commands(msg, params.hostname.get());
		//cout << "action = " << action << endl;

		//if (action != -1)
		master_data.set(msg);		// maybe need to change the name to the param (image_data)
		pub_image_task.publish(msg);

		if (action == START) run_mission.set(true);
		else if (action == PAUSE) run_mission.set(false);
		action = -1;
	}

}


/*
void Robot::send_task(){//Publisher pub_image_task){
	int task = this->params.tasks.get_last_item();
	// maybe only send if it is different than the previous one
	string msg = encode_task();
	pub_image_task.publish(msg);
}
*/
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

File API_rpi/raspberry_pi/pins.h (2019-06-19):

#ifndef PINS_H
#define PINS_H

#define USING_RPI
// To define raspi pins used

// to check the pins run this command on the Pi: gpio readall
// leds 				WiringPi | BCM | Physical | Color used
#define LED_KA 				22	// 	 6 |	31	  |	  green
#define LED_PLAN_NAV		23	// 	13 |	33	  |	  blue
#define LED_LEADER 			24	// 	19 |	35	  |	  yellow
#define LED_TASK 			25	// 	26 |	37	  |	  red 

#endif

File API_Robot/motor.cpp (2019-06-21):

#include "Arduino.h"
#include "motor.h"
#include "pins.h"
#include <cmath>

Motor::Motor(){}

Motor::Motor(int motor){
	_motor=motor;

  	if (_motor==LEFT_MOTOR){
  		_dir_pin=PIN_LEFT_DIR;
  		_pwm_pin=PIN_LEFT_PWM;
  	} else if (_motor==RIGHT_MOTOR) {
  		_dir_pin=PIN_RIGHT_DIR;
  		_pwm_pin=PIN_RIGHT_PWM;
  	}

  	pinMode(_dir_pin, OUTPUT);
  	pinMode(_pwm_pin, OUTPUT);

  	analogWriteFrequency(_pwm_pin,20000);
  	analogWriteResolution(12);
  	

}

void Motor::setVelocity(double velocity){
	_velocity=velocity;

  _pwm=vel2pwm(_velocity);
    

	if ((_velocity<0 && _motor==RIGHT_MOTOR) || (_velocity>=0 && _motor==LEFT_MOTOR)){
		digitalWrite(_dir_pin,LOW);
    _pwm = 4095 - _pwm;
	}else if ((_velocity >= 0 && _motor==RIGHT_MOTOR) || (_velocity<0 && _motor==LEFT_MOTOR)){
		digitalWrite(_dir_pin,HIGH);
	}
		

	analogWrite(_pwm_pin,_pwm);

}

int vel2pwm(double vel){
  
  if (vel<0){
    vel=-vel;
  }
  double result=4095*(1-(double)(vel/MAX_VELOCITY));
  int pwm_result=(int)result;

  return pwm_result;
}

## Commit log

2018-08-27 hello pow, i added left motor
2018-08-28 dc motor is now working
2018-08-28 'calibrate.ino' run to calib. sensors. Menu to navigate done. Functions in 'calibrate.h.cpp'
2018-08-30 new motor library created
2018-08-30 new functions in motor.h and utils.h
2018-08-30 dc motor plus encoder working in example
2018-08-30 ir calibration code finished (missing storing data in txt, csv...)
    [calibrate.cpp]
2018-08-31 try to save in csv
    [test.csv]
2018-09-14 velocity controller added
2018-09-21 I solved the problem I created...
    [utils.cpp]
2018-09-28 IR getDistance(), uint16_t in 'ir' and 'calibration'
2018-09-30 velocity controller changes
2018-10-01 velocity controller compilation errors solved for Motor
    [motor.cpp, velocity_controller.cpp]
2018-10-07 functioning encoders and motors in arduino file
2018-10-07 motor_control_pid + csv
    [motors_openLoop_noCharge.csv]
2018-10-12 imu changes
2018-10-12 new imu library, working fine
2018-10-12 first comm. and plots motor vel.
2018-10-12 removed old arduino codes and added new simple pid
2018-10-24 tests pid, save data
    [motors_openLoop_noCharge_181020_1.csv, motors_openLoop_noCharge_181020_2.csv, motors_openLoop_noCharge_181020_3.csv]
2018-10-24 more motor data and python script to compute motor tf
    [motors_openLoop_noCharge.csv, motors_openLoop_noCharge_181020_1.csv, motors_openLoop_noCharge_181020_2.csv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]
2018-10-26 pid working
2018-11-07 added odometry, working fine but needs some adjusting
2019-03-06 check battery
2019-03-17 robot + aruco codes 2 print
2019-03-25 robot + test coupling
2019-03-31 save and print robot_params, sensors and controllers
2019-04-13 race and stairs, servo not working
    [comm_1.cpp, comm_1.h]
2019-04-13 servo working
2019-04-13 sending battery voltage
2019-04-13 batt in sensors
2019-04-13 batt in sensors1
2019-04-17 set init pose Teensy
2019-04-17 pumpkin update
2019-04-18 print msg to image
2019-04-18 count_drive in teensy
2019-04-22 now running from current position to end node
2019-04-22 fixed problems with initializing camera formats
2019-04-23 pid followline
2019-04-23 push pumpkin changes from monday
2019-04-23 pumpkin mission 0
2019-04-24 pumpkin changes
2019-05-16 correction in test square
    [robot.cpp]
2019-05-17 imu debugged, doesnt work in interrupt function
2019-06-04 ka & run files
    [robots_config.csv]
2019-06-12 compiling with KA & LE, missing to test
    [robots_tests.csv]
2019-06-14 test leds
2019-06-17 test gpio wiringPi
2019-06-17 gpio wiringPi
2019-06-19 test leds potato
2019-06-19 test leds asparagus
2019-06-19 handle Ctrl^C (compile but not working)
    [robot.cpp]
2019-06-19 improve leds and quit with q (keyboard)
2019-06-22 debug le + logging
    [hola_2019-06-22_19:01:48.csv]
2019-06-23 leds blink (no delay), logging, plot (jupyter notebook)
    [test_r1.csv, test_r2.csv, test_r3.csv]
2019-06-25 aruco couple
2019-06-28 aruco coupling working
2019-07-21 tests coupling...
2019-07-21 tests nav
    [test_r1.csv]
